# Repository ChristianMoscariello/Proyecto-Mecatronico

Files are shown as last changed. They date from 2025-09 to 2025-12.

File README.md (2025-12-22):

Logo Institucional

# Universidad Nacional de Lomas de Zamora – Facultad de Ingeniería

## Desarrollo de un dron multirrotor con inteligencia artificial embarcada para deteccion de personas y focos de incendio con cámara RGB y sensor térmico

---

## Introducción / Objetivo

En la Universidad Nacional de Lomas de Zamora, la Facultad de Ingeniería se dedica a la formación de profesionales en diversas ramas de la ingeniería. Este repositorio corresponde al proyecto desarrollado en el área de **Ingeniería Mecatrónica**, como parte del **Proyecto Final de Carrera**.

El objetivo de este proyecto es el **diseño, construcción e integración de un vehículo aéreo no tripulado (UAV) multirrotor**, capaz de ejecutar misiones autónomas de búsqueda mediante **sensado térmico, visión RGB e inteligencia artificial embarcada**, con transmisión de eventos a una estación de control terrestre.

El proyecto busca demostrar la **viabilidad técnica** de una plataforma de bajo costo orientada a tareas de detección temprana, priorizando estabilidad, confiabilidad y modularidad del sistema.

---

## Índice

- Descripción  
- Instrucciones de Uso  
- Tecnologías Utilizadas  
- Listado de Componentes  
- Esquemáticos  
- Fotos / Videos
- Carpetas del Proyecto  
- Autor  

---

## Descripción

Este proyecto se basa en el desarrollo de un **dron multirrotor tipo hexacóptero**, diseñado para realizar misiones autónomas de búsqueda y detección de eventos térmicos y visuales.

El sistema integra:

- Una **plataforma aérea** controlada por un piloto automático (Pixhawk comandado por un ESP32).
- Un **sistema de detección embarcado** basado en Raspberry Pi, encargado del procesamiento de imágenes RGB y térmicas mediante algoritmos de inteligencia artificial.
- Un **microcontrolador ESP32** que actúa como integrador del sistema, coordinando las comunicaciones entre los distintos subsistemas.
- Un enlace de **comunicación LoRa** para la transmisión de eventos relevantes hacia una estación base (*Estación Terrestre*).

La estación terrestre permite definir misiones, visualizar la trayectoria del dron y recibir notificaciones de eventos detectados, incluyendo su localización geográfica.

---

## Instrucciones de Uso

Para utilizar este proyecto, seguir los siguientes pasos generales:

**Paso 1:** Configurar y cargar el firmware correspondiente en el ESP32 y en la controladora de vuelo.

**Paso 2:** Preparar la Raspberry Pi con el sistema operativo y las dependencias necesarias para el procesamiento de imágenes y ejecución de los modelos de IA.

**Paso 3:** Conectar los sensores (cámara RGB y sensor térmico) y verificar su correcto funcionamiento.

**Paso 4:** Ejecutar la aplicación de la Estacion Terrestre desde una computadora en entorno Jupyter, estableciendo la comunicación con el dron mediante el adaptador USB - LoRa.

**Paso 5:** Definir una misión, cargarla en el sistema y realizar las pruebas de vuelo en un entorno controlado.

Asegurarse de contar con los componentes, herramientas y configuraciones detalladas en las secciones siguientes.

---

## Tecnologías Utilizadas

Este proyecto fue desarrollado utilizando las siguientes tecnologías:

### Robótica
- Controladores de vuelo para UAV (Pixhawk)
- Motores brushless y servomotores
- Plataforma multirrotor tipo hexacóptero

### Electrónica
- ESP32
- Sensor térmico (MLX90640)
- Cámara RGB (OV5647)
- Módulos de comunicación LoRa (SX1278)
- Controladores electrónicos de velocidad (ESC)

### Programación
- Python
- C / C++
- Scripts de control y procesamiento

### Plataformas
- MAVLink
- OpenCV
- ONNX Runtime

### Inteligencia Artificial
- Redes neuronales convolucionales
- YOLOv8 para detección de personas y fuego
- Procesamiento de visión por computadora

---

## Listado de Componentes

- Controladora de vuelo Pixhawk
- 6 x ESC de 30 A
- 6 x Motores brushless 2816
- 6 x Hélices 8x4.5 (3 giro derecho y 3 giro izquierdo)
- Batería LiPo 3S 5000 mAh
- Fuente step down XL4015 a 5V
- Microcontrolador ESP32
- Módulo LoRa SX1278
- Servo sg90
- Raspberry Pi  
- Sensor térmico MLX90640  
- Cámara RGB OV5647  
- Chasis impreso en 3D
- 6 x Brazos aluminio portamotores

Para el adaptador USB - LoRa de la base:
- Microcontrolador ESP32
- Módulo LoRa SX1278

---

## Esquemáticos

A continuación se presentan los esquemáticos y diagramas de diseño del sistema:

Esquema eléctrico del dron:

drone

Diagrama en bloques del dron:

Diagrama dron

Esquema eléctrico del adaptador USB-LoRa:

puente

Diagrama en bloques del adaptador USB-LoRa:

Diagrama puente

Diagrama en bloques estación terrestre:

Diagrama gs

## Fotos / Videos

En esta sección se incluyen imágenes y videos correspondientes al desarrollo y funcionamiento del proyecto:

- Fotografías del dron ensamblado


unnamed



fotodron2

- Imágenes de pruebas de vuelo

fotodronvual 

fotodronvula2 

fotodronvuela3

### Demostracion del funcionamiento

Seteo de la mision desde la estacion terrestre, verificacion de envios de datos, vuelo, analisis con resultado negativo y positivo (con imagenes capatadas por camara RGB e infrarroja)

https://drive.google.com/file/d/1ojA_1EPUBh213Cx6VwPE2h_yf2Y8xk58/view?usp=drive_link

https://youtu.be/2DbrhcWoiKQ

---

## Carpetas del Proyecto

La estructura del repositorio es la siguiente:

- **Adaptador USB-LoRa:** Codigo del adapatador para ESP32.
- **Camara termografica:** Codigo utilizado en el M5stick y Raspberry Pi.
- **Codigos camara:** Codigo utilizado para la camara RGB en Rapsberry Pi.
- **Entrenamiento IA:** Imagenes utilizada para entrenar la inteligencia artificial.
- **Esquemas electricos:** Esquemas de los componentes utilizados.
- **Estacion terrestre:** Versiones de la aplicacion de la estacion terrestre, codigo fuente a ejecutar en Jupyter.
- **Funcionando para final - comportameinto full:** Programas definitivos con el comportamiento correcto.
- **Funcionando para regularidad:** Programas con vuelo lineal a un punto.
- **Hojas de datos:** Hojas de datos de los componentes utilizados.
- **Informes:** Documentación técnica, informes, presentacion, cronogramas y material académico relacionado - leer informe e informe complementario.
- **Modelado 3D:** Archivos editables en SolidWorks con el ensamble y piezas del dron.  
- **Pixhawk:** Código fuente del sistema para ESP32.
- **Videos demostracion funcionamiento:** Imágenes y videos del desarrollo y pruebas, videos de misiones.  

---

## Autores

Este proyecto fue realizado por 

**Fernández Malenotti, Ignacio** 
fmalenotti.ignacio@gmail.com

**Moscariello, Christian**
chris_mosca7@hotmail.com

**Yacono, Emiliano**
emilianoyacono@gmail.com

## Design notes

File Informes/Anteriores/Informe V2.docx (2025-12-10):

Sistema de detección autónoma de personas y/o fuego

Para la implementación del sistema de visión y detección, se diseñó una arquitectura de software modular distribuida en tres bloques lógicos principales que operan de manera cooperativa. Esta estructura permite separar las tareas de adquisición de datos en tiempo real del procesamiento computacional intensivo, asegurando que el procesamiento pesado de las imágenes no detenga la ejecución del resto del sistema. Esto permite seguir recibiendo datos de los sensores y mantener la conexión fluida con el dron sin tener que esperar a que finalice cada inferencia de la inteligencia artificial.

Adicionalmente, esta división operativa ofrece una ventaja significativa en la gestión del software: el aislamiento de entornos. Cada código se ejecuta en su propio entorno virtual independiente, lo que evita conflictos entre versiones incompatibles de las mismas librerías. De esta manera, cada subsistema cuenta con las dependencias exactas que necesita, sin que las actualizaciones requeridas por el modelo de IA comprometan la estabilidad de los controladores de los sensores.

El flujo de información comienza en el nivel de hardware con el firmware del M5StickC, el cual actúa como un dispositivo de adquisición dedicado para el sensor térmico. En el siguiente nivel, ejecutándose sobre la Raspberry Pi, el Código 1 (Módulo de captura y análisis térmico) funciona como el orquestador principal: solicita los datos térmicos, captura las imágenes visuales RGB y realiza un primer filtrado de alertas basado en temperatura.

Finalmente, la integración entre la visión clásica y la inteligencia artificial se logra mediante un esquema asíncrono basado en el sistema de archivos. Cuando el Código 1 deposita una imagen en la carpeta compartida, se dispara automáticamente al Código 2 (Análisis con IA). Este último módulo procesa la imagen con el modelo YOLOv8 y, en caso de confirmar una detección positiva, emite las alertas correspondientes al sistema de control, cerrando así el ciclo de vigilancia autónoma detallado en el siguiente esquema global.

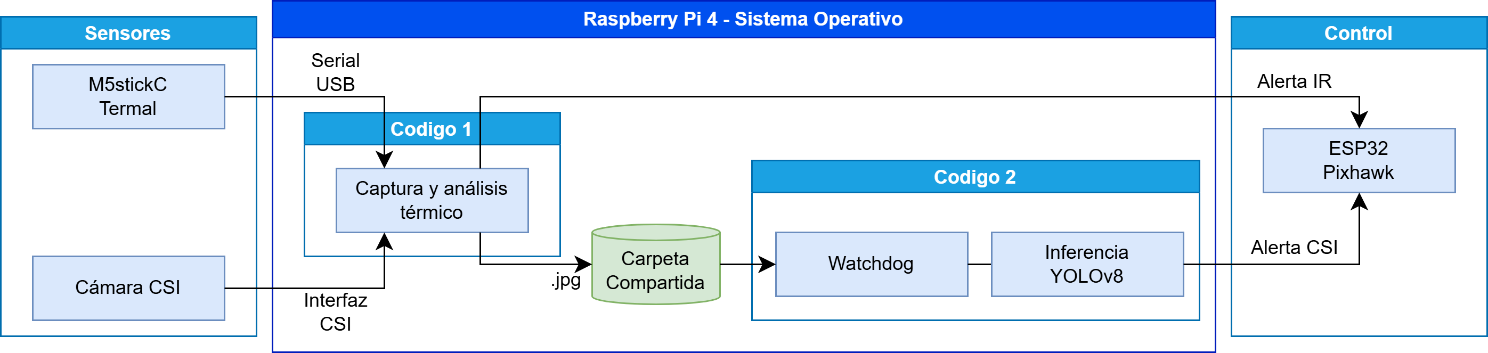
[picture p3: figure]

Descripción del firmware del M5StickC para adquisición térmica

El M5StickC utiliza su módulo ESP32-PICO interno para capturar y transmitir el cuadro térmico proveniente del sensor MLX90640. El firmware implementa un esquema de operación por solicitud (modo pull), en el cual la captura no se realiza de manera continua, sino únicamente cuando la Raspberry Pi envía el comando correspondiente a través del enlace serial USB. Esta lógica permite minimizar el procesamiento interno del dispositivo y evita generar datos innecesarios cuando no están siendo requeridos.

Inicializar pantalla, serial, bus I2C y sensor MLX90640

Al iniciar, el sistema configura la pantalla del M5StickC, el bus I2C utilizado para comunicarse con el sensor y la interfaz serial que enlaza el módulo con la Raspberry Pi. También se inicializa el MLX90640 con los parámetros de funcionamiento seleccionados: modo intercalado, resolución de 18 bits y una frecuencia de actualización de 2 Hz. En caso de que el sensor no responda, el dispositivo detiene su ejecución y muestra un mensaje de error para evitar el envío de información incorrecta.

Iniciar captura térmica

Una vez completada la configuración, el M5StickC permanece a la espera de un comando entrante. Si la Raspberry Pi envía la cadena "GET_FRAME", el firmware inicia la lectura completa del sensor y obtiene la matriz de 768 valores de temperatura. Luego, estos datos se redondean a dos decimales y se empaquetan en un documento JSON que contiene un único arreglo con todas las mediciones, manteniendo el orden original de la matriz del sensor.

Limpiar buffer serial y enviar JSON

Para asegurar una transmisión limpia, el firmware limpia el buffer serial antes de enviar la respuesta y encapsula el mensaje JSON entre dos delimitadores (#START y #END). Esto permite que la Raspberry Pi detecte con precisión el inicio y el fin del paquete, incluso si el flujo serial contiene ruido o interrupciones temporales. Finalmente, el dispositivo actualiza la pantalla para indicar el envío y vuelve al estado de espera hasta recibir el próximo comando.

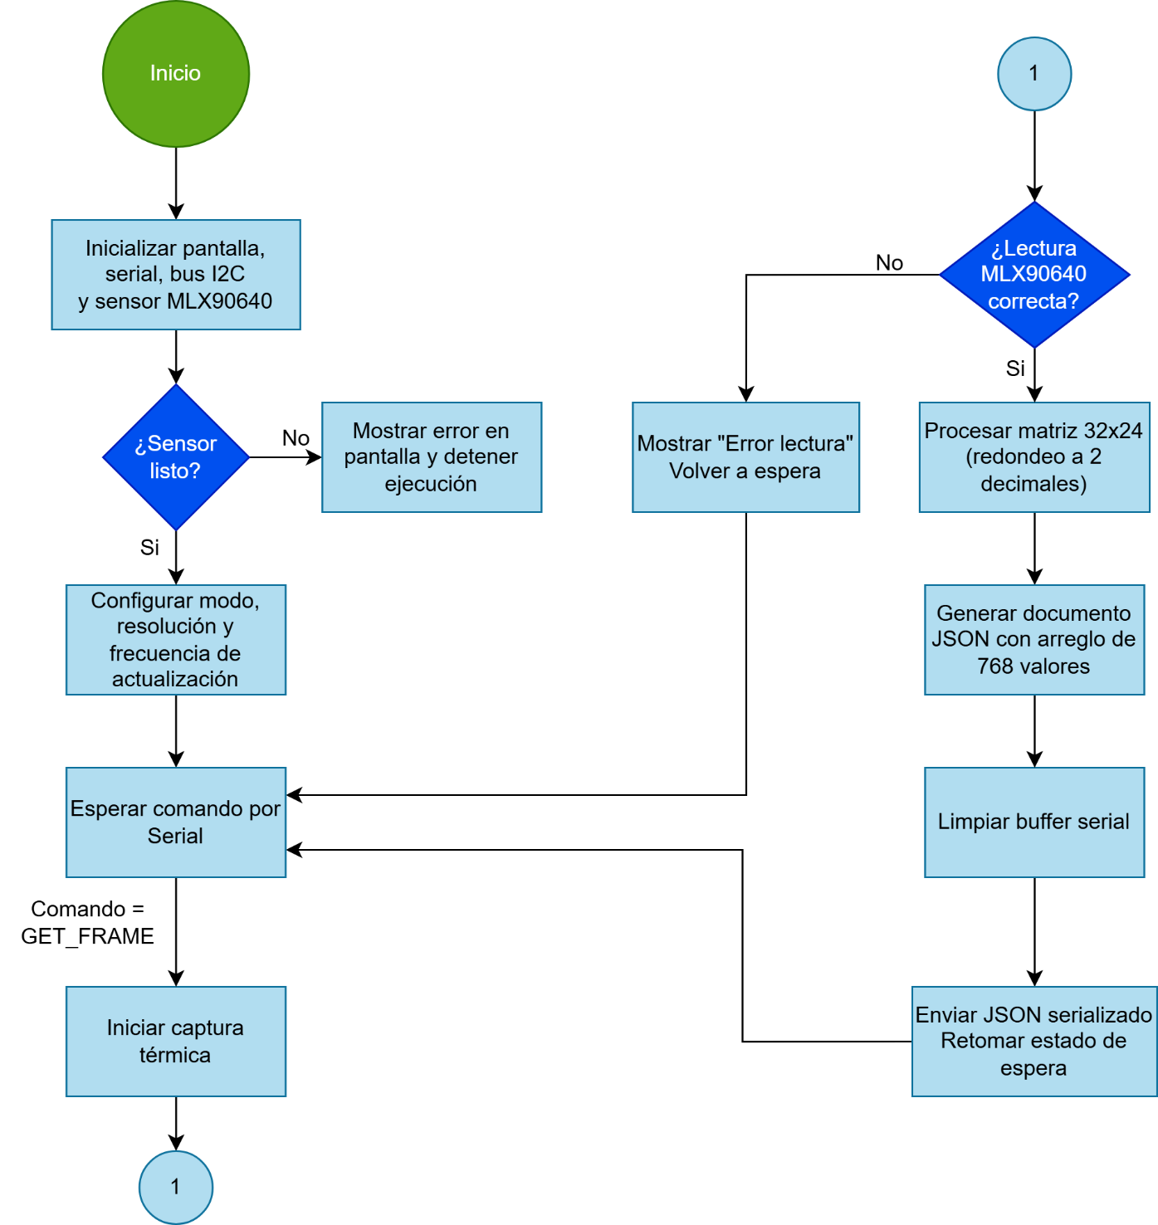
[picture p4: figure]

Descripción técnica del módulo de captura y análisis térmico

El módulo de captura y análisis térmico, implementado en el programa “codigo1_camaras_v2.py”, constituye el núcleo funcional del subsistema de visión del dron, integrando captura de imágenes, análisis térmico en tiempo real y comunicación bidireccional con los dispositivos embarcados (M5StickC con sensor térmico y ESP32 para las órdenes de vuelo). En su diseño se prioriza la fiabilidad operativa, la trazabilidad de eventos y la capacidad de ejecutar detección autónoma sin intervención del operador.

Inicialización Serial/Carpetas/Cámara

El código se estructura en torno a una clase de configuración centralizada que define todos los parámetros relevantes para la ejecución: puertos seriales, velocidades de comunicación, características de la cámara CSI, umbrales térmicos para la detección de personas e incendios, y rutas de almacenamiento. Esta centralización permite mantener un control claro sobre los elementos críticos del sistema.

Una vez iniciada la aplicación, el sistema crea y valida automáticamente las carpetas de trabajo y habilita un esquema de registro persistente de métricas y eventos, pensado para documentar tanto condiciones normales de funcionamiento como situaciones de error.

Modo de toma de imágenes

En cuanto a la adquisición sensorial, el módulo establece dos canales de comunicación independientes. Por un lado, se conecta al M5StickC con su sensor MLX90640 integrado, responsable de transmitir matrices térmicas de 32×24 píxeles, encapsuladas en formato JSON. Por el otro, se vincula con la ESP32, que puede iniciar el proceso de captura mediante el comando STABLE o recibir mensajes de alerta cuando el sistema identifica una anomalía térmica. Ambos enlaces operan con tolerancia a fallos y emplean hilos independientes cuando es necesario, garantizando que la recepción de comandos no interfiera con el procesamiento de imágenes.

El procesamiento térmico constituye el corazón computacional del módulo. Cada frame recibido es sometido a un filtrado de mediana para reducir ruido y mejorar la coherencia espacial de la matriz. Luego se ejecuta un análisis basado en segmentación por umbral adaptativo: el sistema determina dinámicamente la temperatura de fondo y la contrasta con rangos característicos para personas y focos de incendio. Los rangos de temperatura y área utilizados para discriminar entre personas y focos de incendio se definen durante la inicialización del sistema y provienen de pruebas de campo realizadas previamente, lo que permite adaptar el algoritmo a condiciones reales.

En paralelo a la recepción y procesamiento del frame térmico, el software coordina la toma de imágenes RGB con una cámara OV5647 de 8MP y las mismas son guardadas con el mismo sello temporal que la térmica para facilitar su análisis conjunto. Las imágenes RGB se almacenan en la carpeta “imágenes_visual” para que sean relevadas por el código que analizará a las mismas utilizando inteligencia artificial.

Resultados del análisis térmico

Se utilizan técnicas de etiquetado de componentes conectados para identificar regiones candidatas, evaluando su área y delimitándolas con recuadros que representan las detecciones en la matriz térmica. Esta metodología permite operar incluso en condiciones de ruido térmico elevado y evita falsos positivos derivados de objetos ambientales cálidos pero no relevantes.

Una vez identificadas las regiones de interés, el módulo genera una imagen térmica interpretada mediante un mapa de calor (heatmap), señalando visualmente las detecciones mediante los recuadros codificados por color. Finalmente, cuando el sistema determina la presencia de una persona o un posible foco ígneo, se activa el protocolo de alerta hacia la ESP32, enviando una cadena JSON minimalista que sirve como disparador para acciones de navegación o marcación de eventos en el dron.

El ciclo de operación permite dos modos de activación: captura manual mediante teclado o activación remota desde la ESP32. Esto habilita tanto pruebas en laboratorio como funcionamiento autónomo durante un vuelo real. Cada ciclo concluye retornando un estado de éxito o error y dejando registrada toda la actividad en los archivos de log correspondientes.

En conjunto, este módulo implementa una arquitectura de software orientada a la confiabilidad y la detección temprana, combinando visión térmica, control asincrónico de hardware y generación de evidencia visual. Es el componente responsable de transformar datos brutos del sensor infrarrojo en información estructurada y accionable, funcionando como la primera etapa de interpretación del entorno en el sistema completo del dron.

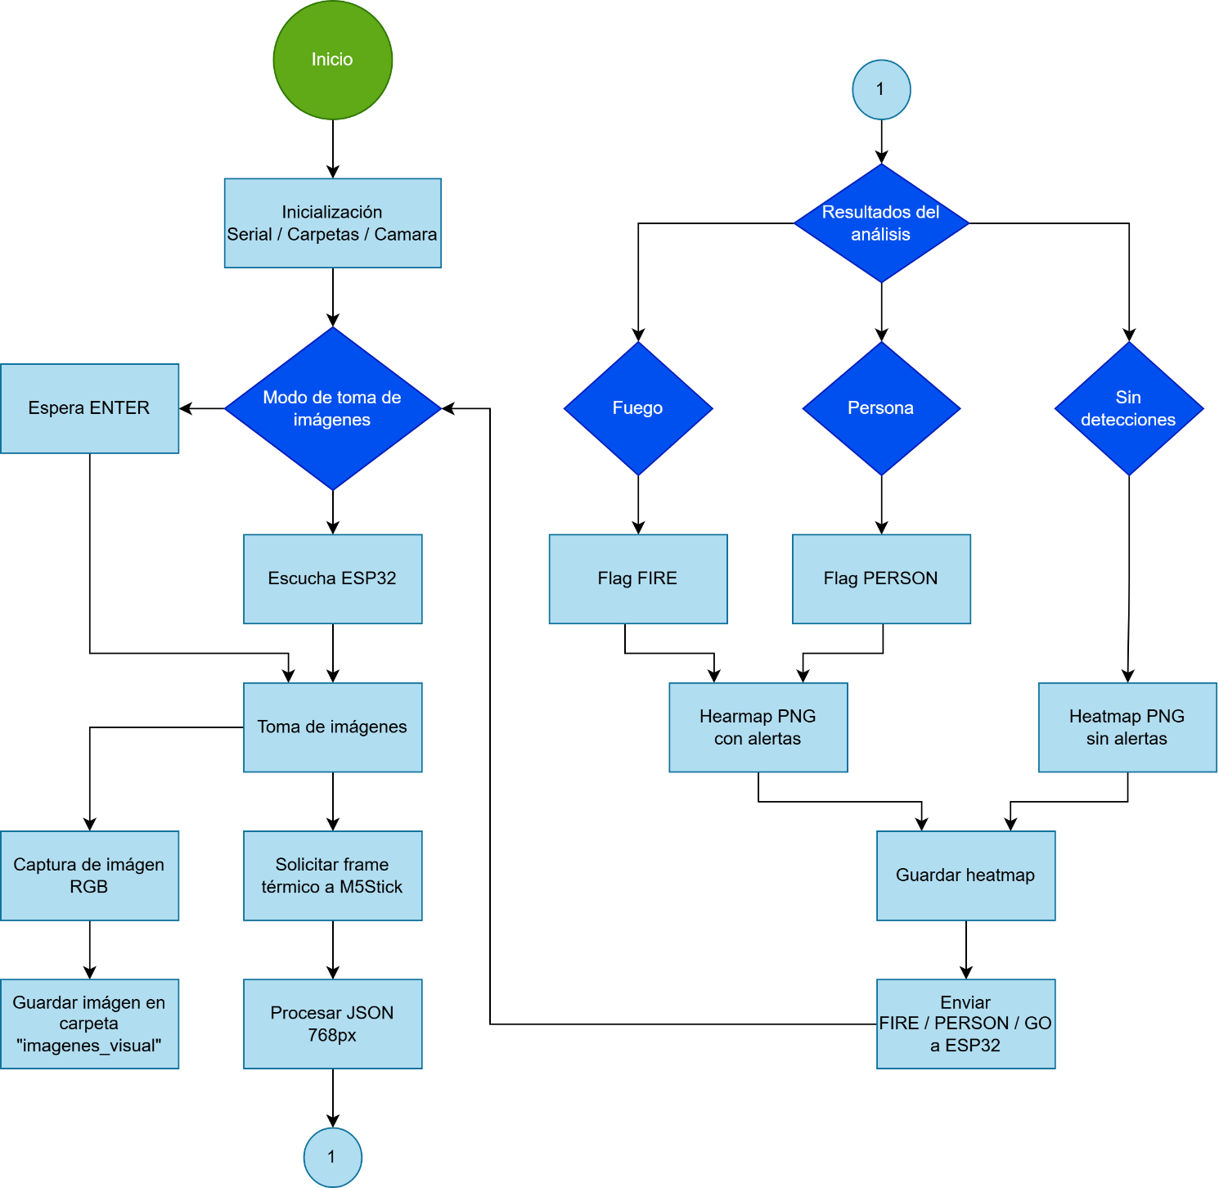
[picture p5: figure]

Descripción técnica del módulo de análisis de imágenes con inteligencia artificial

El segundo módulo del sistema, codigo2_ia_v3.py, cumple el rol de núcleo inteligente del pipeline general. Mientras el Código 1 se ocupa de adquirir imágenes RGB y almacenarlas de manera ordenada, este módulo funciona como un observador activo que espera la llegada de esos archivos para someterlos a un análisis automático mediante un modelo de detección basado en YOLOv8 exportado a ONNX. De esta manera, Código 2 permite cerrar el ciclo completo: captura, procesamiento inteligente y emisión de alertas al dron o al sistema embebido encargado de actuar en consecuencia.

Un aspecto clave del diseño es que todo el análisis de imágenes se realiza de manera local, sin depender de servicios externos ni de una conexión estable a Internet. Esto responde a una limitación propia del sistema: la comunicación entre el dron y la base se establece mediante LoRa, un protocolo de largo alcance pero muy baja tasa de transferencia, insuficiente para enviar imágenes o ejecutar análisis de imágenes de manera remota. Al ejecutar la inteligencia artificial directamente en la Raspberry embarcada sobre el dron, mismo puede operar de forma autónoma y generar alertas inmediatas sin necesidad de enlaces WiFi o satelitales, lo que mejora la robustez del sistema y lo vuelve apto para entornos aislados o con conectividad limitada.

Configurar sistema (carpetas, paths, clases)

El programa inicia estableciendo una configuración centralizada que define los directorios relevantes, los parámetros y el modelo a utilizar. A diferencia del primer módulo, aquí el objetivo no es solo verificar y organizar carpetas, sino también garantizar un entorno de ejecución preparado para alojar tanto las imágenes procesadas como los registros de funcionamiento.

Esta etapa crea las carpetas necesarias, carga el nombre del modelo ONNX y fija los umbrales mínimos de confianza para descartar predicciones irrelevantes. Al igual que Código 1, este módulo también mantiene comunicación con la ESP32, enviando alertas de detección o indicaciones para continuar la exploración.

Carga de modelo YOLOv8 ONNX

El corazón del módulo se concentra en la clase AnalizadorIA, encargada de cargar el modelo YOLOv8 en formato ONNX y llevar adelante el flujo completo: desde la preparación de la imagen, pasando por el análisis del modelo, hasta la interpretación final de las detecciones.

Durante el proceso, las imágenes se redimensionan, normalizan y convierten al formato requerido por el modelo. Luego, las predicciones se reescalan al tamaño original y se construyen los recuadros delimitadores junto con sus etiquetas correspondientes.

Una decisión de diseño destacada es la definición explícita de las clases (“Persona”, “Fuego”, “Humo”), agrupando fuego y humo bajo una misma categoría de alerta (FIRE) para simplificar la comunicación operativa con el dron.

Iniciar vigilancia (watchdog en carpeta)

Sobre este analizador se apoya el componente responsable de reaccionar a los eventos del sistema de archivos. Utilizando la biblioteca watchdog, el módulo monitoriza en tiempo real la carpeta de salida del Código1. Cada vez que aparece una nueva imagen, el código procesa el archivo, lo somete al análisis del modelo y genera una imagen anotada con las detecciones encontradas. Esta imagen se guarda con un registro de fecha y hora preciso, lo que facilita la trazabilidad y el alineamiento temporal con los registros del resto del sistema.

Resultados del análisis

La lógica de alertas también reside en este módulo. Cuando no se detectan objetos relevantes, el sistema informa a la ESP32 mediante el mensaje “GO”, manteniendo el flujo de confirmaciones del estado general. Por el contrario, si se identifican personas, fuego o humo, se emiten alertas específicas (“PERSON” o “FIRE”), habilitando al dron a reaccionar de acuerdo con la situación.

Finalmente, el ciclo completo del sistema se encapsula en la clase SistemaIA. Una vez en ejecución, el módulo entra en un estado de escucha permanente y solo se detiene ante una interrupción explícita del usuario. Al finalizar, todos los recursos se liberan de manera ordenada, asegurando un cierre limpio tanto de la conexión serial como del proceso del watchdog.

En conjunto, este módulo observa, interpreta y actúa, conectando el análisis visual avanzado con una lógica operacional liviana pero efectiva. Su diseño apunta a la fiabilidad y a la eficiencia, respetando el flujo general del proyecto y complementando las capacidades del Código1 para conformar un sistema coherente de vigilancia automática.

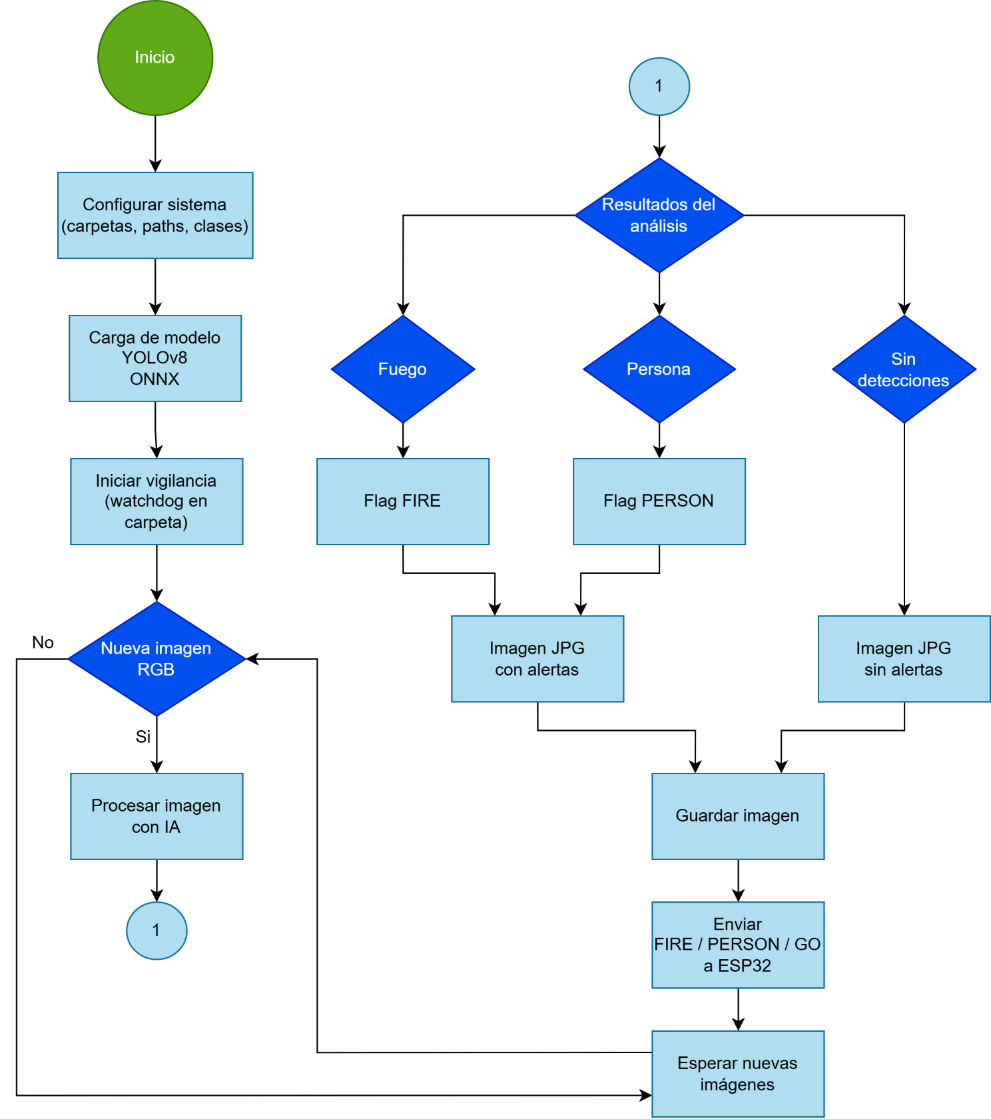
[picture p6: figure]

Facultad de Ingeniería Universidad Nacional de Lomas de Zamora

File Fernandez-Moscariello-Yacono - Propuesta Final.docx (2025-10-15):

PROYECTO FINAL MECATRONICA

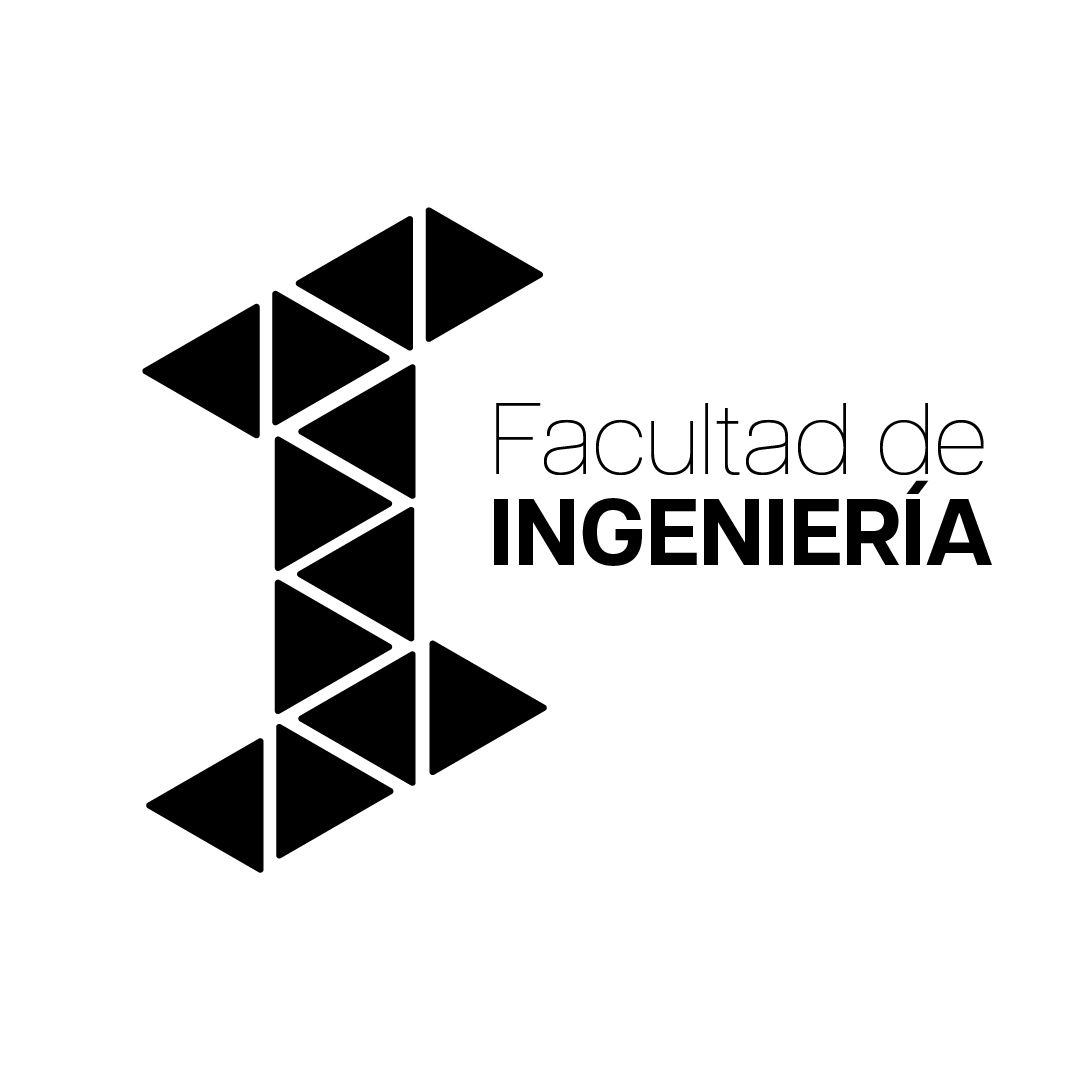
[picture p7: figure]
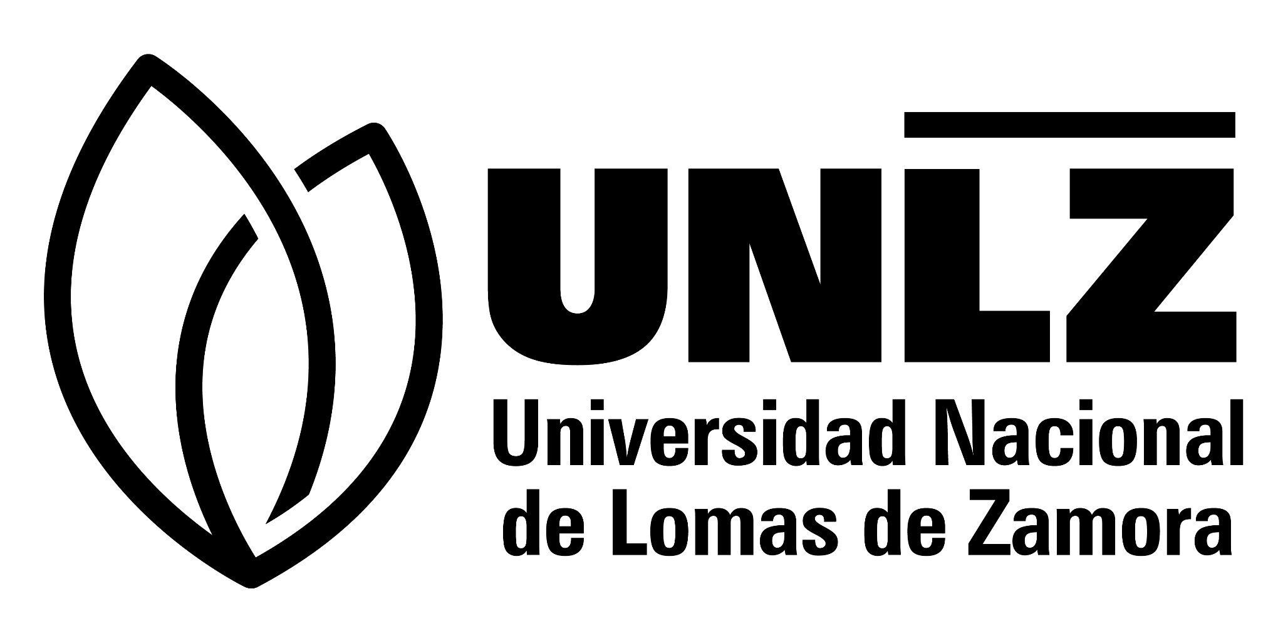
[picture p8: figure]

Profesores:

Ing. Blanca, Ezequiel

Ing. Lukaszewicz, Cristian Leandro

Ing. Szombach, Juan Ignacio

Alumnos:

Fernandez Malenotti, Ignacio

Moscariello, Christian

Yacono, Emiliano

# Propuesta Final

## Título del Proyecto

Dron Autónomo para Detección de Incendios y Rescate de Personas

## Motivación y Antecedentes

Durante el verano, zonas de parques nacionales y áreas de montaña enfrentan dos problemáticas críticas:

1. La aparición de focos de incendio, que pueden propagarse rápidamente debido a la vegetación seca.
2. El extravío de personas en zonas de difícil acceso, como bosques y áreas montañosas.

Actualmente, la cobertura de grandes extensiones con personal reducido dificulta las tareas de vigilancia, control y rescate. Esto retrasa la respuesta inicial ante un incendio o la localización de personas, aumentando riesgos y daños. Además, el coste de patrullaje de un helicóptero es elevado y su espacio aéreo de observación acotado.

## Descripción de la Propuesta

Se propone el desarrollo de un prototipo de dron autónomo a escala, capaz de:

1. Detectar visual y térmicamente focos de incendio en su etapa inicial.
2. Localizar personas extraviadas mediante análisis de imagen e infrarrojo.
3. Transmitir coordenadas precisas a los equipos de intervención.
4. Transportar pequeñas cargas, como materiales para iniciar la extinción de focos o suministros de supervivencia y primeros auxilios.

El proyecto se centra en mostrar la viabilidad técnica de un sistema aéreo no tripulado para inspeccionar grandes superficies de forma rápida y eficiente, incluso en zonas de difícil acceso terrestre.

## Alcance

En la presentación final se podrá mostrar:

1. El dron volando y detectando de forma representativa un foco de incendio o una persona.
2. El sistema de sujeción de pequeñas cargas (prototipo).
3. Transmisión de coordenadas y visualización de imágenes térmicas o simuladas.

Limitaciones:

- La capacidad de carga estará restringida por el tamaño y peso del dron prototipo.
- La parte de extinción o entrega de suministros será demostrativa, no a escala real por razones de peso y seguridad.

- No está contemplada la navegación en interiores ni que pueda sortear autónomamente obstáculos, puesto que no contará con sensor de tipo radar 3D debido a restricciones monetarias y temporales en el desarrollo.

Escenario de uso

- Parques provinciales, nacionales, etc., campos privados y todo tipo de establecimiento donde se requiera patrullaje activo en época de peligro de incendios.
- Parques provinciales, nacionales, etc. y cualquier ubicación donde se practique treking u otra actividad que lleve a personas a áreas remotas y de difícil acceso, dónde puedan perderse o sufrir un accidente y por lo consiguiente necesiten ser ubicadas en el menor periodo de tiempo posible.
- Para un mejor aprovechamiento de la tecnología se propone el uso de múltiples drones, con la finalidad de poder rastrillar simultáneamente mayor superficie de terreno.

## Docentes para Consultas

- Catedra de procesamiento de señales: uso de filtros y diversas formas de usar sensores para obtener señales en su forma más representativa.
- Catedra de mecánica de los fluidos: cálculo de fuerzas de empuje y sustentación.
- Catedra de modelado y dinámica de sistemas mecánicos: modelado de estructuras, fuerzas y cargas

Especificación de requerimientos

- Auto pilotaje: Mediante un sistema de coordenadas GPS dinámico y un acelerómetro, el dron deberá realizar una ruta de vuelo tipo rastrillaje y volver al punto de origen al finalizar.
- Procesamiento de imágenes térmicas: Utilizando un sensor IR deberá ser capaz de detectar focos de anormalidad térmica.
- Procesamiento de imágenes RGB: Utilizando una cámara y una inteligencia artificial correctamente entrenada alojada en un Raspberry pi, el dron deberá detectar de qué se trata el foco de anomalia térmica (principio de incendio, persona perdida, animal).
- Transporte de kit de auxilio: En caso de que se este buscando una persona y la misma sea encontrada, mediante un sistema tipo gripper/dropper se le proporcionará un kit de primera contingencia.

Diseño funcional

Arquitectura general:

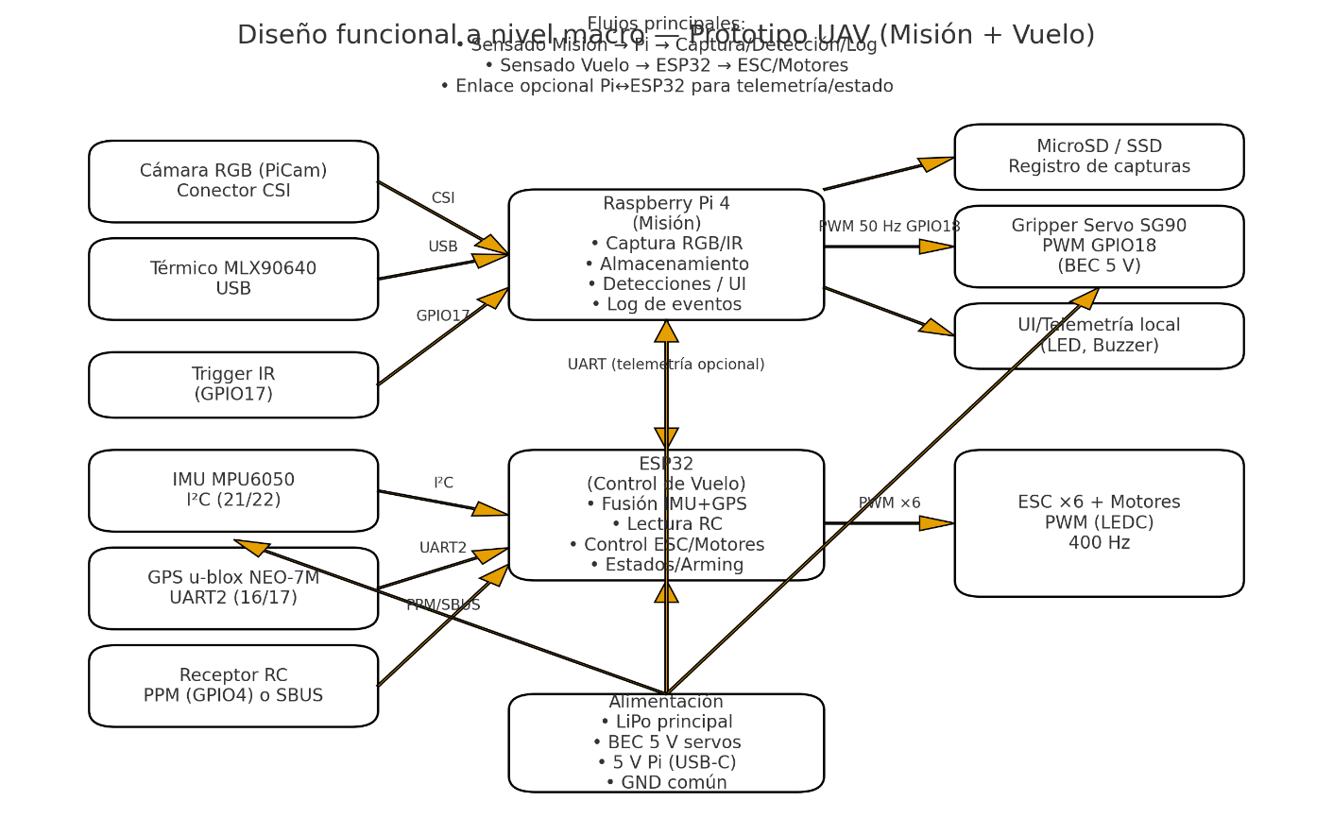
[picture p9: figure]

Conexionado individual:

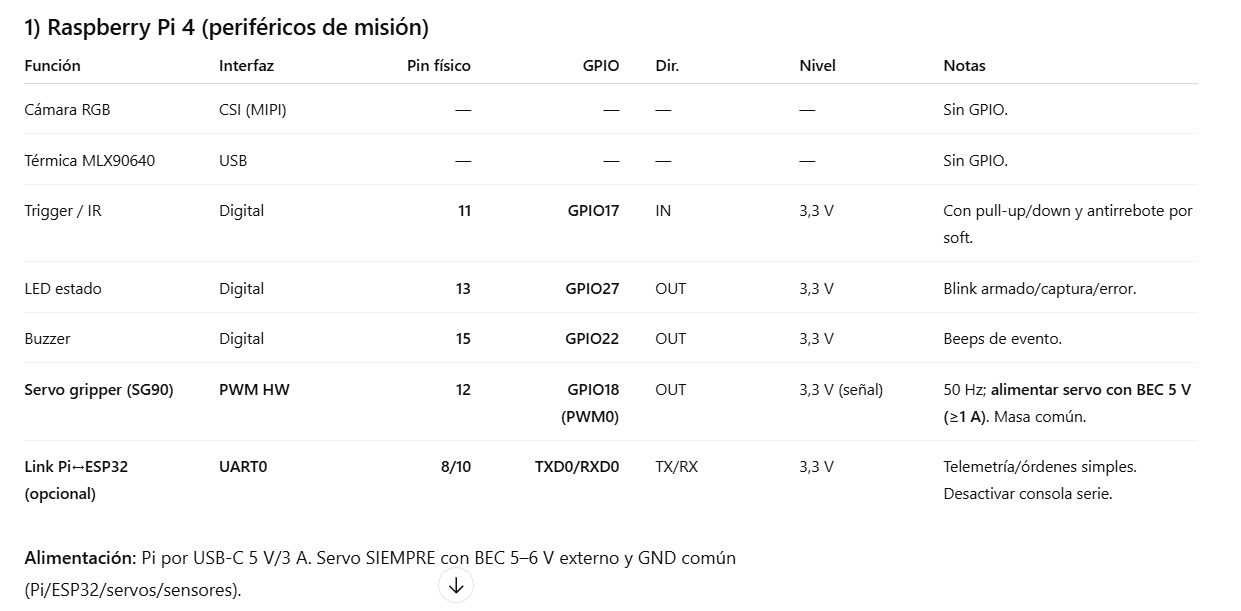
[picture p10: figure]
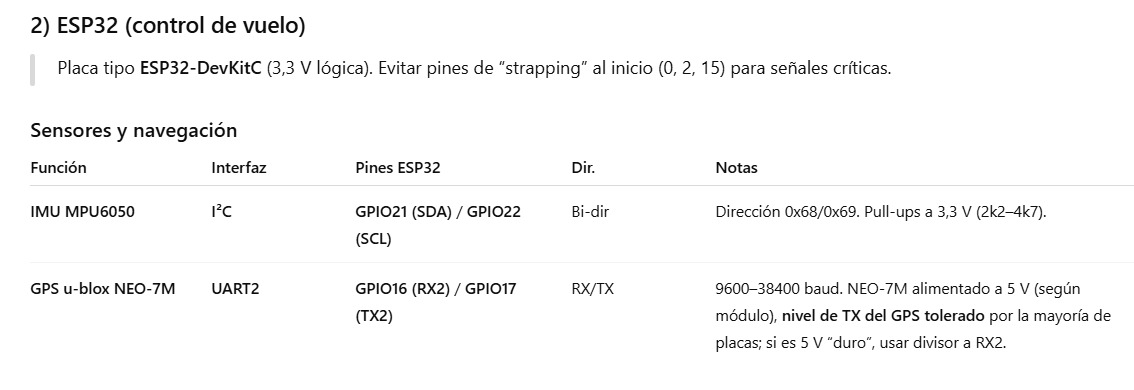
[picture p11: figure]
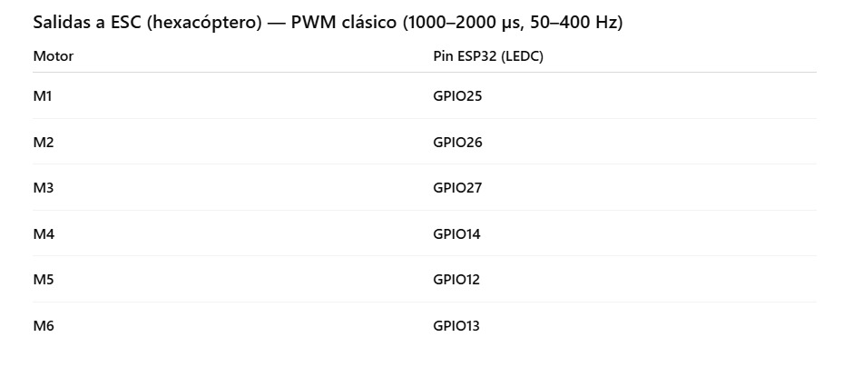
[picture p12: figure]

Lista de materiales y costos

Ítem | Cantidad | Precio unitario | Precio total
Motor brushless + ESC 30A + Helice | 6 | 50000 | 300000
Batería LiPO 3S | 1 | 70000 | 70000
ESP32 | 1 | 10000 | 10000
Kit NAZA M V2 | 1 | 160000 | 160000
Estructura (caños aluminio + placas conectoras) | 1 | 40000 | 40000
Cámara térmica IR | 1 | 180000 | 180000
Raspberry pi 4 | 1 | 100000 | 100000
Cámara RGB | 1 | 35000 | 35000
Rollo filamento PETG | 1 | 18000 | 18000
Miscelaneos (tornillería, cables, luces) | 1 | 15000 | 15000
Total | | | 928000

Universidad Nacional de Lomas de Zamora Facultad de Ingeniería

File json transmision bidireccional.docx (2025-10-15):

PC → Dron (Comandos enviados desde la estación)
Comando (t) | Ejemplo d completo | Descripción
MISSION_COMPACT | json { "p": [[-34.6037, -58.3816], [-34.6040, -58.3820], [-34.6030, -58.3830]], "h": [-34.6035, -58.3810], "a": 30, "s": 10, "event_action": "VOLVER" } | Envía misión compacta con polígono, HOME, altitud, espaciamiento y acción tras evento
RETURN | {} | Ordena al dron regresar a HOME
ARM | {} | Arma el dron para vuelo
DISARM | {} | Desarma el dron
TRIM | json { "accel": 128, "roll_lr": 128, "roll_fb": 128, "rudder": 128, "switch": 128 } | Envía trims configurados desde la GUI
GET_TRIMS | {} | Solicita los valores de trims al dron
GRIPPER | { "state": "OPEN" } | Abre o cierra el gripper

Dron → PC (Mensajes recibidos por la estación)
Comando (t) | Ejemplo d completo | Descripción
TELEMETRY | json { "lat": -34.6037, "lon": -58.3816, "alt": 32, "speed": 12, "heading": 90, "battery": 85, "status": "ARMED", "current_wp": 2, "total_wp": 5 } | Telemetría en tiempo real del dron
STATUS | { "message": "Misión iniciada" } | Estado general o respuesta de comando
WP_REACHED | { "wp_number": 2 } | Indica que se alcanzó un waypoint
DEBUG | { "message": "Sensor OK" } | Mensaje de depuración del dron
FIRE | { "lat": -34.6040, "lon": -58.3820 } | Detección de fuego, marcador en mapa
PERSON | { "lat": -34.6050, "lon": -58.3830 } | Detección de persona, marcador en mapa
TRIM_DATA | json { "accel": 128, "roll_lr": 128, "roll_fb": 128, "rudder": 128, "switch": 128 } | Respuesta con valores actuales de trims

Raspberry ➜ ESP32
Comando (t) | Ejemplo d completo | Descripción
FIRE | {} | Detección de fuego
PERSON | {} | Detección de persona

Ejemplos:

{ "t": "FIRE", "d": { }, "ts": 0}

{ "t": "PERSON", "d": { }, "ts": 0}

ts: timestamp, enviar cero

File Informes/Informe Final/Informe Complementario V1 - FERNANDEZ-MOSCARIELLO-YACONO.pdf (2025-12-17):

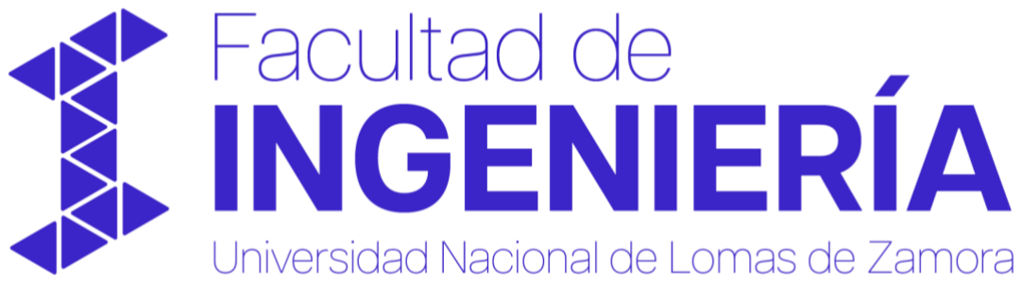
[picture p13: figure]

# PROYECTO EN INGENIERÍA MECATRÓNICA

# Dron autopilotado con detección de fuego y personas mediante procesamiento IA de cámaras INFORME COMPLEMENTARIO

## Integrantes:

- FERNANDEZ MALENOTTI, Ignacio | DNI: 42.043.463
- MOSCARIELLO, Christian | DNI: 37.053.307
- YACONO, Emiliano | DNI: 34.485.253

## Docentes:

## - Ing. Blanca, Ezequiel - Ing. Lukaszewickz, Cristian - Ing. Szombach, Juan

### Facultad de Ingeniería

Universidad Nacional de Lomas de Zamora

Índice

Ya teniendo en claro qué debe hacer el gripper se establecen una serie de

1.Introducción

En este informe complementario se buscará dar una mirada más teórica a la constitución física del dron: se analizarán temas como qué es un dron, qué tipos existen, por qué vuelan, qué fuerzas interactúan en los mismos y demás. Se ejemplifica con el prototipo construido y se repasan técnicas y diseño del mismo.

1.1. Contexto del proyecto

En los últimos años, los vehículos aéreos no tripulados (UAV) han adquirido una relevancia creciente en aplicaciones de monitoreo, inspección y asistencia en entornos de difícil acceso. En particular, los drones multirrotor ofrecen ventajas significativas en términos de maniobrabilidad, despegue vertical y capacidad de vuelo estacionario. Todo esto, enfocado hacia la búsqueda de personas desaparecidas e inicios de focos de incendio.

1.2. Objetivo general del sistema

El objetivo general del sistema desarrollado es diseñar e implementar un dron multirrotor capaz de ejecutar misiones autónomas de exploración dentro de un área delimitada, incorporando capacidades de detección de eventos y actuación física sobre el entorno.

1.3. Metodología de desarrollo

El desarrollo del prototipo se realizó siguiendo una metodología de diseño iterativa, propia de un proyecto experimental, en la cual se combinaron etapas de análisis teórico, selección de componentes, fabricación de piezas y validación mediante pruebas prácticas.

### 2. Concepto general de vehículo aéreo no tripulado (UAV)

2.1. Definición de dron / UAV

Un vehículo aéreo no tripulado (Unmanned Aerial Vehicle), es una aeronave capaz de funcionar sin un piloto a bordo, su control puede realizarse de manera remota u operar de forma autónoma utilizando sensores y sistemas electrónicos on board.

En términos de ingeniería, un UAV forma parte de un sistema más amplio que incluye sensores, actuadores, sistemas de control, comunicación y una estructura física diseñada para soportar las cargas aerodinámicas y operacionales durante el vuelo.

2.2. Clasificación de drones

Los UAV pueden clasificarse según distintos criterios, siendo uno de los más relevantes el tipo de plataforma aérea utilizada para generar sustentación y control de vuelo.

2.2.1. Ala fija

Los drones de ala fija generan sustentación a partir del movimiento relativo del aire sobre la superficie alar, de manera similar a una aeronave convencional. Este tipo de plataformas se caracteriza por una alta eficiencia energética en vuelos de larga distancia y mayor autonomía.

Sin embargo, requieren una velocidad mínima para mantenerse en vuelo, lo que implica la necesidad de pistas de despegue, catapultas o sistemas de lanzamiento, lo que implica también, una pista con sensores y una mayor complejidad al momento de despegue/aterrizaje.

Este tipo de drones no permiten vuelo estacionario.

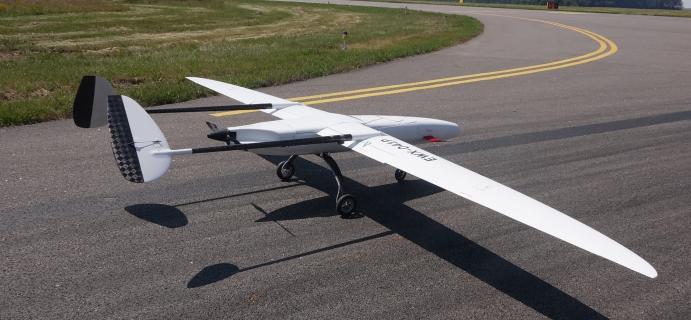
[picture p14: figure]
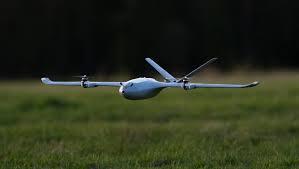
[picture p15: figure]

Dron de ala fija.

2.2.2. Multirrotores

Los drones multirrotor utilizan múltiples hélices dispuestas alrededor de un chasis para generar empuje vertical de manera directa. El control del movimiento se logra mediante la variación de la velocidad angular de cada motor, permitiendo controlar los ejes de roll, pitch y yaw sin superficies aerodinámicas móviles (flaps, alerones como poseen los drones de ala fija).

Entre sus principales características se destacan la capacidad de despegue y aterrizaje vertical, el vuelo estacionario y una elevada maniobrabilidad, lo que los hace especialmente adecuados para misiones de precisión y operación en espacios reducidos.

Los drones con redundancia de motores (6 u 8) pueden llegar a continuar un vuelo o hacer un aterrizaje de emergencia sin suponer una caída inmediata en caso de que alguno de los mismos falle.

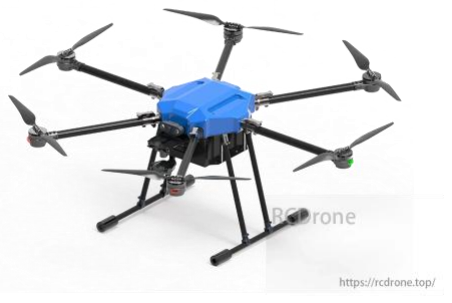
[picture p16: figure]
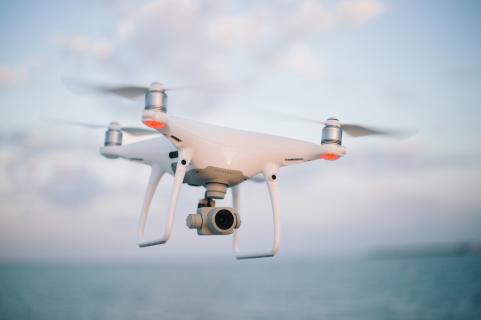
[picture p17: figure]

Dron multirrotor.

2.2.3. Comparación y elección del multirrotor

Si bien los UAV de ala fija presentan ventajas en términos de eficiencia y alcance, sus limitaciones operativas los hacen poco adecuados para misiones que requieren vuelo estacionario, maniobras precisas y operación en áreas delimitadas.

En el contexto del presente proyecto, orientado a tareas de exploración, detección y asistencia en un área específica, la configuración multirrotor resulta la opción más adecuada, ya que permite un control preciso de la posición y la capacidad de detenerse sobre un punto de interés.

Característica | Ala fija | Multirrotor
Despegue vertical | No | Si
Vuelo estacionario | No | Si
Autonomía | Alta (1 motor) | Baja (+ 4 motores)
Precisión | Baja | Alta
Complejidad mecánica | Alta | Media
Adecuado para ayuda | Limitado por precisión | Óptimo
2.3. Aplicaciones típicas (búsqueda, monitoreo, rescate)

Los UAV multirrotor se emplean ampliamente en aplicaciones donde se requiere acceso rápido, operación remota y adquisición de información en tiempo real. Entre las aplicaciones más relevantes se encuentran las tareas de búsqueda y rescate, monitoreo ambiental, inspección de estructuras inseguras y asistencia en situaciones de emergencia.

La capacidad de integrar sensores especializados para la tarea y realizar misiones autónomas convierte a estas plataformas en herramientas eficaces y eficientes para la exploración de zonas de difícil acceso o potencialmente peligrosas para humanos.

### 3. Fundamentos físicos del vuelo

El vuelo de un dron multirrotor se basa en la generación de empuje aerodinámico mediante hélices rotativas que interactúan con el aire circundante. Desde el punto de vista de la aerodinámica, una hélice puede modelarse como un disco actuador (teorema de Froude y Betz) que imparte una variación de cantidad de movimiento a una masa de aire, generando una fuerza de reacción que permite sostener y maniobrar el vehículo

A diferencia de las aeronaves de ala fija, donde la sustentación se produce por el desplazamiento horizontal, en los multirrotores el empuje se genera principalmente en dirección normal al plano de rotación de las hélices, permitiendo el vuelo estacionario.

3.1. Principio de sustentación

En drones multirrotor, la sustentación está directamente asociada al empuje producido por las hélices, el cual puede analizarse mediante la teoría de cantidad de movimiento aplicada a un disco actuador.

3.1.1. Flujo de aire y generación de empuje

La hélice puede considerarse un mecanismo destinado a generar una fuerza capaz de mover un vehículo inmerso en un fluido. Desde el punto de vista físico, se trata de un ala que gira alrededor de un eje, impulsada por un motor, impartiendo un pequeño incremento de velocidad a una gran masa de aire que atraviesa el plano de rotación

Según la segunda ley de Newton, el empuje generado por la hélice es consecuencia del cambio de cantidad de movimiento del aire:

T = m ∗ ΔV

donde el caudal másico de aire atravesando el disco depende del área del mismo y de la velocidad inducida en el flujo.

3.1.2. Diferencia de presiones

El modelo de disco actuador establece que, al atravesar el plano de la hélice, el aire experimenta un salto de presión. Aguas arriba del disco, el aire posee una presión y velocidad determinadas, mientras que al cruzar el disco se agrega energía al flujo en forma de un incremento de presión ∆p, asociado al trabajo realizado por el motor

El empuje generado por el disco puede expresarse como:

T = A ∗ Δp

siendo A el área del disco actuador. Este enfoque permite vincular directamente el empuje con la variación de presión inducida por la hélice.

3.1.3. Relación con hélices rotativas

Una hélice real no es un disco continuo, sino un conjunto de palas que pueden interpretarse como elementos de ala rotativa. Cada sección radial de la pala contribuye al empuje total, y la suma de estas contribuciones a lo largo del radio reproduce el comportamiento global del disco actuador

La teoría de pala-elemento confirma que una hélice eficiente es aquella que transfiere poca energía cinética a una gran masa de aire, minimizando pérdidas.

3.2. Fuerzas actuantes sobre el dron

Durante el vuelo, el dron se encuentra sometido a un conjunto de fuerzas externas que determinan su equilibrio y movimiento.

3.2.1. Sustentación (Lift)

En el caso del multirrotor, la sustentación se identifica con el empuje total generado por las hélices. Esta fuerza actúa aproximadamente normal al plano de rotación y es consecuencia directa de la aceleración del aire hacia abajo producida por los rotores.

3.2.2. Peso

El peso es la fuerza gravitatoria que actúa sobre el dron y se expresa como:

P = m ∗ g

Esta fuerza incluye la masa de la estructura, los sistemas electrónicos, la batería y la carga útil

3.2.3. Arrastre (Drag)

El arrastre aerodinámico se opone al movimiento relativo del dron respecto al aire. Si bien su influencia es reducida en vuelo estacionario, cobra importancia durante desplazamientos horizontales y maniobras dinámicas.

3.2.4. Empuje (Thrust)

El empuje es la fuerza generada por las hélices al impartir energía al flujo de aire. Desde el punto de vista del modelo de cantidad de movimiento, el empuje total se obtiene del balance entre el flujo de masa y la variación de velocidad inducida en el aire al atravesar el disco actuador

3.3. Equilibrio de fuerzas en vuelo estacionario
3.3.1. Condición de hover

El vuelo estacionario se produce cuando el dron permanece suspendido sin aceleración vertical. En esta condición, el empuje total generado por los rotores equilibra exactamente el peso del sistema:

Ttotal = P

3.3.2. Requerimiento de empuje total

La teoría de cantidad de movimiento muestra que, para maximizar la eficiencia, el incremento de velocidad impartido al aire debe ser pequeño. Sin embargo, en aplicaciones reales se requiere un margen de empuje adicional para maniobras y control.

Por este motivo, en drones multirrotor se diseña el sistema de propulsión para que el empuje máximo total sea al menos el doble del peso del vehículo.

3.3.3. Distribución del empuje en multirrotores

En vuelo estacionario ideal, el empuje se distribuye uniformemente entre los N rotores:

Ti =

P
N

Durante maniobras, el controlador de vuelo modifica esta distribución para generar momentos alrededor de los ejes del dron.

3.4. Dinámica básica del multirrotor
3.4.1. Control de roll, pitch y yaw

El control del multirrotor se basa en la generación de momentos mediante diferencias de empuje entre los rotores. No se emplean superficies aerodinámicas móviles, sino variaciones en la velocidad angular de las hélices.

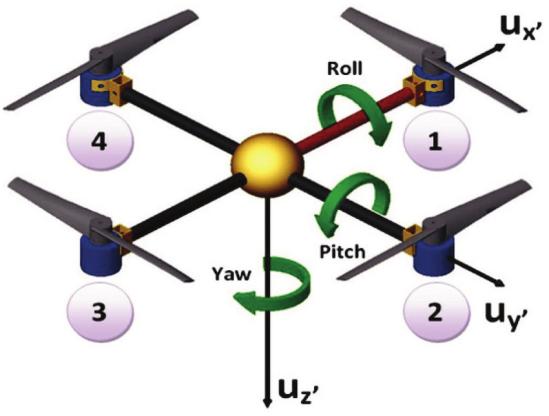
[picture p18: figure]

Referencia de | movimientos del dron
multirrotor.
3.4.2. Variación de velocidades angulares

La teoría de pala-elemento indica que el empuje de una hélice depende aproximadamente del cuadrado de su velocidad angular:

T ≃ α

2

Esto permite un control preciso del movimiento mediante pequeñas variaciones en la velocidad de los motores

3.4.3. Par reactivo y compensación

Cada hélice genera un par reactivo opuesto a su sentido de giro. Para evitar la rotación no deseada del dron sobre el eje vertical, los multirrotores utilizan hélices que giran en sentidos opuestos, compensando los torques individuales.

El control del yaw se logra modificando el balance de torque entre los grupos de hélices de giro horario y antihorario.

3.5. Empuje máximo y carga útil máxima
3.5.1. Condición mínima para despegar y hacer hover
Para condición de vuelo estacionario (hoover), la condición de equilibrio vertical es:

ΣT = P = m ∗ g
Donde:
ΣT = empuje total [N]
P = peso [N]
m = masa
g = gravedad

El dron en orden de marcha:

P = 2,15 kg ∗ 9,81 m/s2 = 21,1N

3.5.2. Modelo de empuje estático de hélice (aproximación) Estimamos el empuje estático con el coeficiente de empuje Ct:

T = Ct ∗ ρ ∗ n

2
∗ D

4
Donde:
T = empuje de una hélice [N]
Ct = coeficiente de empuje estático, dependiendo de la hélice varía entre 0,08 a 0,12 ρ = densidad del aire a nivel del mar = 1,125 kg/m3
D = diámetro de la hélice [M]
n = revoluciones por segundo (RPS)

Se conoce que:
- Diámetro de hélices es 8” → 0,2032 M
- Los motores giran 12000 RPM a 12V → n = 200 RPS

Calculamos:
ρ ∗ n

2 ∗ D

4 ≃ 83,54
Entonces:
T = Ct ∗ 83,54
3.5.3. Empuje máximo estimado (por motor y total)
El coeficiente Ct real corresponde a cada fabricante de hélices y es propio de generar diversas curvas dependiendo de la configuración hélice/motor elegidos.

Para la combinación de motor y hélice del dron, un valor realista es Ct = 0,1:
- Empuje por motor: 0,85 kgf
- Empuje total del dron: 5,11 kgf
3.5.4. Carga útil máxima (a empuje máximo)
En condiciones ideales, sin pérdidas ni factores externos:

Carga máxima = (ΣT) − P dron = 5,11 kg − 2,15 kg = 2,96 kg

La carga máxima teórica que puede transportar el dron es de 2,96 kg.

Esto en situaciones reales depende de la carga de la batería y de condiciones climáticas, sumando que no es recomendable volar a carga máxima debido a que no deja resto para maniobras imprevistas, lo que puede ocasionar accidentes.

Es buena práctica aplicar un coeficiente de seguridad para situaciones reales de 2 por lo menos, dejando la carga real operable en el rango de 1,5 kg.

### 4. Arquitectura física del dron desarrollado

La arquitectura física del sistema fue definida priorizando la estabilidad en vuelo, la modularidad, la facilidad de mantenimiento y la integración de sensores y actuadores adicionales.

4.1. Configuración general del prototipo

El prototipo se basa en una configuración multirrotor de seis motores (hexacóptero), seleccionada por su mayor capacidad de carga, redundancia y estabilidad frente a fallas parciales, en comparación con configuraciones de cuatro rotores.

La configuración general incluye:

- Estructura central portante (chasis)
- Brazos radiales con motores brushless en los extremos
- Sistema de propulsión compuesto por motores, hélices y ESC
- Sistema de control de vuelo
- Sistema de distribución de alimentación
- Sensores de navegación y detección
- Sistema mecánico de gripper para liberación de carga
- Cámaras montadas sobre base antivibratoria
4.2. Disposición de componentes

La disposición de los componentes fue seleccionada con el objetivo de minimizar interferencias mecánicas, eléctricas y electromagnéticas, así como de optimizar el balance del vehículo frente a las oscilaciones propias del movimiento del dron.

De forma general:

- Motores y hélices se ubican en los extremos de los brazos, generando un brazo de palanca adecuado para el control de actitud.
- ESC se montan próximos a cada motor, reduciendo la longitud de los cables de potencia y las pérdidas por efecto Joule.
- La batería se posiciona en medio del centro geométrico del chasis, debido a que es el elemento más pesado del dron y no debe generar tendencias al desbalance.
- Controlador de vuelo (Pixhawk) se monta sobre el eje central del dron, para que el sensado del acelerómetro y giróscopo sea correcto.

- Las cámaras se colocan en la parte inferior del dron, montadas en una base antivibratoria. Se orientan hacia abajo, para poder realizar capturas de elementos a nivel del suelo.
- El gripper se monta en una posición central inferior, alineado con el eje vertical del dron para evitar momentos indeseados durante la liberación de carga.

La disposición responde a criterios funcionales y dinámicos, buscando que las fuerzas y momentos generados durante el vuelo no introduzcan comportamientos no deseados.

4.3. Centro de masa y balanceo

El centro de masa del dron constituye un parámetro crítico para la estabilidad y el desempeño del sistema de control.

En el prototipo desarrollado, se buscó que el centro de masa coincida lo más posible con el centro geométrico del chasis, y se encuentre alineado con el eje vertical que pasa por el controlador de vuelo.

Para lograrlo, se aplicaron los siguientes criterios:

- Ubicación central de la batería, como componente de mayor masa.
- Simetría en la distribución de motores, brazos y ESC.
- Montaje alineado del gripper y de las cámaras.
- Posibilidad de ajuste longitudinal de la batería para correcciones finas.

Un centro de masa correctamente ubicado reduce:

- El esfuerzo de control requerido por los motores.
- El acoplamiento indeseado entre los ejes de roll, pitch y yaw.
- Las | oscilaciones | durante | vuelo | estacionario | y | maniobras | lentas.
4.4. Distribución estructural del chasis

El chasis del dron cumple simultáneamente funciones estructurales y de integración de sistemas.

Su diseño se basa en una estructura central rígida, de la cual parten los brazos que soportan los motores.

Las principales características de la distribución estructural son:

- Brazos radiales diseñados para soportar esfuerzos de flexión y torsión generados por el empuje de los motores.
- Cuerpo central donde se introducen los brazos y se realiza el montaje del controlador de vuelo.
- Base que se fija al cuerpo central, la misma alberga a la batería en posición central, es soporte de las patas y es donde se colocan los soportes de placas.
- Soportes de placas destinados a ubicar la Raspberry Pi y la placa con el ESP32 y el módulo LoRa. A su vez en los extremos se atornilla el soporte de cámaras y gripper.
- Soporte de gripper y base antivibratoria de cámaras (sobre la cual luego van fijadas las mismas).

La estructura fue concebida para ser liviana pero rígida, priorizando una buena relación resistencia–peso, fundamental para maximizar la autonomía del sistema.

### 5. Selección del sistema de propulsión

El sistema de propulsión constituye el subsistema central del dron, ya que es el encargado de generar el empuje necesario para el vuelo, permitir el control de la actitud y sostener la carga útil del vehículo.
Su selección se realizó considerando los requerimientos de empuje total, eficiencia energética, confiabilidad y compatibilidad con la arquitectura general del prototipo.
5.1. Motores brushless
5.1.1. Principio de funcionamiento

Los motores brushless de corriente continua (BLDC) utilizados en drones son máquinas eléctricas síncronas de imanes permanentes, en las cuales el rotor contiene imanes y el estator está compuesto por bobinados trifásicos.

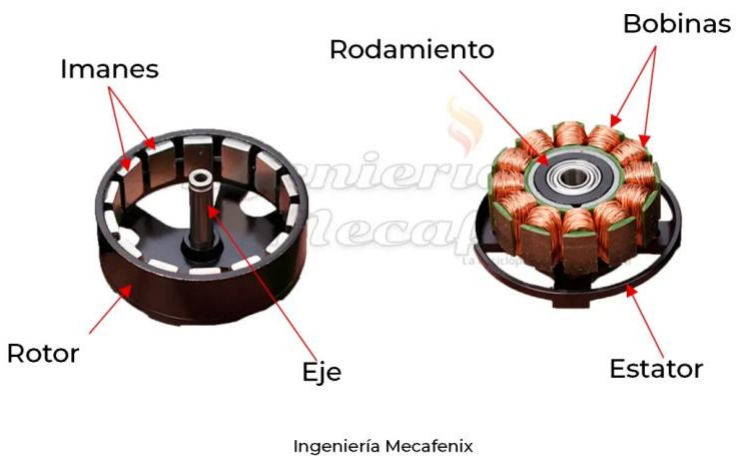
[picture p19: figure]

Componentes motor brushless

A diferencia de los motores con escobillas, la conmutación de corriente no se realiza de forma mecánica sino electrónicamente mediante un ESC, lo que permite:

- Mayor eficiencia
- Mayor vida útil
- Mejor control de velocidad
- Reducción del mantenimiento

El par generado por el motor produce la rotación de la hélice, transformando energía eléctrica en energía mecánica y, posteriormente, en energía cinética del flujo de aire.

5.1.2. Parámetro KV y su significado

El parámetro KV de un motor brushless indica la velocidad angular que el motor alcanza por cada volt aplicado en vacío:

KV =

RPM
Volt

Un motor con mayor KV gira a más revoluciones por voltio, mientras que uno con menor KV gira más lentamente pero es capaz de mover hélices de mayor diámetro y paso.

KV bajo → hélices grandes, mayor empuje, mejor eficiencia

KV alto → hélices pequeñas, mayor velocidad, menor eficiencia en hover

La selección del KV debe realizarse considerando el voltaje de la batería y el tipo de hélice a utilizar.

5.1.3. Criterios de selección de motores

Los principales criterios utilizados para la selección de los motores del prototipo fueron:

- Empuje máximo por motor, suficiente para sostener el peso del dron con margen.
- Compatibilidad con hélices de gran diámetro, favoreciendo la eficiencia.
- Corriente nominal adecuada, para no exceder las capacidades del ESC.
- Relación empuje–peso favorable, reduciendo masa total.
- Disponibilidad comercial, considerando el contexto de prototipado y las restricciones temporales de la cursada.

A nivel de diseño, se buscó que el empuje máximo total del sistema sea al menos el doble del peso total del dron, asegurando capacidad de maniobra y estabilidad.

5.1.4. Motores utilizados en el prototipo

El prototipo utiliza seis motores brushless modelo 2816, montados en configuración hexacóptero.
Este tipo de motor presenta:
- Tamaño adecuado para hélices de 8 pulgadas
- Buen compromiso entre par y velocidad

- Capacidad de generar empuje suficiente con tensiones de 3S (11,1V - 12,6V)
- Uso extendido en drones de tamaño medio

La elección de seis motores aporta redundancia y una mayor capacidad de carga respecto a configuraciones de cuatro rotores.

5.2. Controladores electrónicos de velocidad (ESC)
5.2.1. Función del ESC

El ESC (Electronic Speed Controller) es el encargado de convertir la tensión continua de la batería en señales trifásicas, controlando la velocidad del motor mediante modulación PWM.

Permiten ajustar con precisión la velocidad de cada motor para controlar la actitud del dron.

5.2.2. Corriente nominal y margen de seguridad

La corriente nominal del ESC debe ser superior a la corriente máxima esperada del motor bajo carga.

Como criterio de diseño, se adopta un margen de seguridad del 20 al 30%, tal que:

I ESC ≥ 1,3 ∗ I motor

Este margen reduce el riesgo de sobrecalentamiento y aumenta la confiabilidad del sistema durante maniobras exigentes.

5.2.3. Compatibilidad con motores y batería

La compatibilidad entre ESC, motor y batería se evaluó considerando:

- Tensión nominal de operación (3S)
- Corriente máxima admisible
- Frecuencia de respuesta
- Soporte para protocolo estándar de utilizado por el controlador de vuelo
5.2.4. ESC utilizados en el prototipo

En el prototipo se emplearon ESC de 30 A, uno por cada motor.

5.3. Hélices
5.3.1. Diámetro y paso

Las hélices se caracterizan principalmente por:

- Diámetro: determina el volumen de aire acelerado
- Paso: distancia teórica que avanzaría la hélice en una rotación completa

Hélices de mayor diámetro desplazan una mayor masa de aire a menor velocidad, lo que resulta más eficiente para vuelo estacionario.

5.3.2. Influencia en empuje y consumo

Según la teoría de cantidad de movimiento, es más eficiente generar empuje acelerando una gran masa de aire a baja velocidad que una pequeña masa a alta velocidad.

En consecuencia:

Hélices grandes → mayor empuje, menor consumo en hover

Hélices pequeñas → mayor consumo para igual empuje

La elección de hélice impacta directamente en la autonomía del dron.

5.3.3. Hélices de giro horario y antihorario

Cada hélice genera un par reactivo opuesto a su sentido de giro.

Para compensar este efecto, el dron utiliza hélices de giro horario (CW) y de giro antihorario (CCW), distribuidas alternadamente, permitiendo el equilibrio de torques y el control del yaw.

Si se colocaran todas las hélices iguales, los pares no se anularían y el dron giraría sobre su eje.

5.3.4. Hélices seleccionadas y justificación

El prototipo utiliza hélices 8×4,5 pulgadas, alternando de giro horario para motores impares y giro antihorario para los pares.

Esta selección se justifica por:

- Compatibilidad con motores 2816
- Buen compromiso entre empuje y consumo
- Disponibilidad comercial
- Adecuadas para tensiones de 3S

El conjunto motor–hélice permite generar el empuje necesario para el vuelo estacionario con un margen adecuado para maniobras.

### 6. Sistema de alimentación eléctrica

El sistema de alimentación eléctrica del dron es el encargado de suministrar la energía necesaria para el correcto funcionamiento de todos los subsistemas.
Su correcta selección impacta directamente en la autonomía, la capacidad de carga, la seguridad y la confiabilidad del sistema.

En un dron multirrotor, la batería constituye uno de los componentes de mayor masa, por lo que su elección representa un compromiso entre energía disponible y peso total del vehículo.

6.1. Tipos de baterías para drones
6.1.1. LiPo

Las baterías de polímero de litio (LiPo) son ampliamente utilizadas en drones debido a su elevada densidad de potencia, lo que les permite entregar corrientes muy altas en períodos cortos.

Sus principales características son:

- Alta tasa de descarga (C elevado), capacidad de suministrar grandes corrientes instantáneas
- Formato plano y liviano
- Uso extendido en aplicaciones RC y UAV

Como desventajas, presentan:

- Mayor sensibilidad a sobrecargas y descargas profundas
- Requerimientos estrictos de carga y balanceo
- Vida útil reducida si no se operan correctamente
6.1.2. Li-ion

Las baterías de ion de litio (Li-ion), como las celdas 18650 o 21700, se caracterizan por una mayor densidad energética, aunque con una menor capacidad de entrega de corriente en comparación con las LiPo.

Sus principales ventajas son:

- Mayor energía por unidad de masa
- Mayor vida útil
- Mejor estabilidad térmica

Sin embargo, presentan limitaciones importantes en drones multirrotor:

- Tasa de descarga más baja
- Menor capacidad para responder a picos de corriente
- Se debe colocar una configuración en paralelo para lograr corrientes de descarga comparables a las de una celda LiPo individual.

Por este motivo, su uso es más común en drones de largo alcance o configuraciones optimizadas para vuelo eficiente.

6.2. Parámetros eléctricos
6.2.1. Tensión nominal (S)

La tensión nominal de una batería se expresa mediante la cantidad de celdas conectadas en serie, indicadas como S.

Cada celda de litio presenta una tensión nominal aproximada de 3,7 V. A plena carga, 4,2 V.

Por ejemplo:

3S → 11,1 V nominal / 12,6 V a plena carga

4S → 14,8 V nominal / 16,8 V a plena carga

La tensión seleccionada debe ser compatible con los motores, ESC y electrónica del dron.

6.2.2. Capacidad (mAh)

La capacidad de la batería indica la cantidad de carga eléctrica que puede suministrar y se expresa en miliamperios-hora (mAh).

Una mayor capacidad permite mayor autonomía, pero también implica un aumento de masa, lo que incrementa el consumo y puede contrarrestar el beneficio energético.

6.2.3. Tasa de descarga C

La tasa de descarga C indica la corriente máxima que la batería puede suministrar de forma segura, y se define como:
Imax = C ∗ Capacidad

Por ejemplo, la batería utilizada de 5000 mAh con una tasa de 60C puede entregar

Imax = 60 ∗ 5A = 300A

6.3. Análisis de consumo y autonomía
6.3.1. Consumo estimado por motor

El consumo de cada motor depende del empuje requerido, la hélice utilizada y la tensión de alimentación.

En vuelo estacionario, cada motor genera aproximadamente:

Ti =

P
N

donde N es la cantidad de motores.

En esta condición, el consumo es significativamente menor al consumo máximo nominal del motor. Debido a que los movimientos del dron son considerados suaves, nos acercamos más a este consumo ideal que al máximo.

6.3.2. Consumo total del sistema

El consumo total del dron se obtiene de la suma de:

- Consumo de motores
- Consumo de controladora
- Consumo de microprocesadores
- Consumo de cámaras
- Consumo servo gripper

En la práctica el consumo de los motores es superlativamente mayor al resto de los componentes.

6.3.3. Autonomía teórica y práctica

La autonomía teórica la podemos calcular como:

t =

Capacidad útil de batería
I promedio

Sin embargo en situaciones reales no es posible utilizar el 100% de la capacidad de la batería, existen pérdidas eléctricas y aerodinámicas, se realizan maniobras que aumentan el consumo y otras situaciones, lo que nos lleva a asumir que la autonomía práctica puede ser del 80% de la calculada.

6.4. Batería utilizada en el prototipo
6.4.1. Justificación de elección - cálculo de tiempo de vuelo estimado

El prototipo utiliza una batería LiPo 3S de 45000 mAh con tasa de descarga 60C.

Para no sobre descargar y arruinar la batería suponemos un 80% de capacidad:

Cap usable = 0,8 ∗ 5Aℎ = 4Aℎ

Cálculo de corriente en hoover (sustentación en el lugar)

Empuje total requerido:

Ttotal ≃ m ∗ g = 2,15 kg ∗ 9,81 m/s2 ≃ 21,1N

Empuje por motor (6 motores):

Tmotor ≃

21,1 N
6

≃ 3,52N ≃ 0,36 kgf

Como no tenemos la curva en banco de empuje del motor con hélice (empuje vs corriente consumida), vamos a suponer un consumo razonable de 30A + 3A de electrónica.

Suponiendo una distancia media de navegación entre waypoints de 10 metros, el dron recorre en:

t nav =

10 m
Vel [s]

El tiempo en hoover:

t ℎoover = 3 segundos

Lógicamente el consumo de corriente es algo mayor durante la navegación, usamos:

Inav ≈ 1,15 ∗ Iℎoov

Consumo por tramo en Ah:

Aℎ tramo =

Inav ∗ Tnav
3600s

+

Iℎoov ∗ Tℎoov
3600s

El momento de despegue y aterrizaje tambien suponen consumos considerables, por lo que descontamos un 10% de la bateria en cuestion de reserva:

Aℎ efectiva para tramos = 0,9 ∗ 4Aℎ = 3,6 Aℎ

Máxima cantidad de waypoints posibles:

- Si hay N waypoints hay N-1 tramos
- Hay N hoovers (uno por wp)

Consumo total:

Aℎ(N) =

Inav ∗ Tnav ∗ (N − 1)
3600s

+

Iℎoover ∗ Tℎoover ∗ N
3600s

+ Aℎ reserva

Se busca el máximo N tal que Aℎ ≤ 4Aℎ

Navegando a velocidad de 5 m/s → N ≈ 74 waypoints

Navegando a velocidad de 3 m/s → N ≈ 58 waypoints

Tiempo de vuelo asociado

N waypoints:

t total ≈ N ∗ 3s + (N − 1) ∗

10m
v

Navegando a velocidad de 5 m/s → N ≈ 74 waypoints → 368 segundos ≈ 6,1 m

Navegando a velocidad de 3 m/s → N ≈ 58 waypoints → 364 segundos ≈ 6,1 m

La variabilidad de estos cálculos puede ser muy amplia debido a que el dron puede verse afectado por condiciones climatológicas que dificulten el vuelo, o variaciones en la misión tales como el espaciado entre waypoints, que para el fin del cálculo se establece en 10 metros. La carga del paquete del gripper también afectará en gran porcentaje a la autonomía.

6.4.2. Ventajas y limitaciones

Ventajas:

- Alta capacidad de descarga
- Respuesta rápida ante cambios de carga
- Simplicidad de integración

Limitaciones:

- Autonomía limitada en comparación con soluciones Li-ion
- Requiere cuidados durante carga, almacenamiento y operación
- Degradación acelerada si se exceden los límites operativos

Estas limitaciones son aceptables en el contexto de un prototipo experimental, donde se prioriza la confiabilidad del empuje y la capacidad de maniobra.

### 7. Métodos de manufactura del prototipo

7.1. Enfoque de prototipado rápido

La fabricación del prototipo funcional se basó en el ciclo diseño-fabricación-prueba pudiendo evaluar situaciones reales antes de hacer un diseño definitivo. Ajustes de integración de las partes y para facilitar el mantenimiento fueron hechos sobre la marcha, tales como huecos en el cuerpo para poder conectar cable USB para cargar el programa al ESP32, o bien un sistema de sujeción rápida para la batería.

7.1.1. Iteración y validación

El proceso seguido puede resumirse en las siguientes etapas:

1. Diseño inicial en CAD de los componentes estructurales.
2. Fabricación rápida (impresión 3D).
3. Montaje y pruebas funcionales (ajuste de posiciones de motores y electrónica, verificación de interferencias mecánicas).
4. Evaluación de rigidez y vibraciones.
5. Correcciones de diseño en función de los resultados obtenidos.
6. Nueva fabricación de las piezas modificadas.

Este ciclo se repitió hasta obtener piezas con la solidez y funcionalidad esperadas.

7.1.2. Ventajas frente a manufactura industrial

En comparación con métodos industriales tradicionales (mecanizado CNC, inyección, prfv), el prototipado rápido con el ciclo de iteración CAD - impresión 3D ofrece:

- Reducción significativa de costos iniciales.
- Menor tiempo entre iteraciones.
- Libertad geométrica para integrar electrónica y cableado.
- Facilidad para realizar modificaciones sin rehacer el conjunto completo.

En contraparte, no es un método fácilmente escalable, debido a la poca velocidad de producción de las piezas.

7.2. Fabricación del chasis
7.2.1. Diseño CAD

El chasis fue diseñado íntegramente mediante herramientas de diseño asistido por computadora (CAD), lo que permitió:

- Definir con precisión la geometría del dron.
- Integrar desde el inicio los puntos de fijación de motores, electrónica de control, batería, gripper y cámaras
- Evaluar el ensamblaje completo antes de la fabricación, tomando importante relevancia, debido a que poder analizar las interacciones entre todos los componentes permitió reducir los ciclos de iteración de prototipado.

El uso de CAD también facilitó la exportación directa de los modelos a formato compatible con impresión 3D, reduciendo errores de interpretación durante la manufactura.

7.2.2. Materiales seleccionados para la confección del prototipo

El dron está constituido íntegramente de impresión 3D y aluminio, logrando un excelente y apropiado balance entre peso y rigidez, sin estorbar la normal operativa del mismo.

Los seis brazos que sujetan a los motores y ESC fueron realizados en tubo cuadrado de aluminio 6061, en medida 12mm x 12 mm x 0,7 mm de espesor. Otorgan gran resistencia con poco volumen (respecto de una pieza de similares características mecánicas realizada en impresión 3D) lo que es crucial para no obstruir el flujo de aire creado por las hélices y perder rendimiento.

El resto del chasis del dron fue impreso íntegramente con filamento PETG ya que encontramos múltiples ventajas en el uso de este material:
- El costo es similar al del PLA
- Facilidad de impresión y adherencia a la cama - poco y nulo warping respecto a ABS
- Excelente capacidad mecánica y alta tenacidad
- Temperatura de fusión más alta que PLA, lo que permite trabajarlo con herramientas manuales para ajuste fino, y no tener que volver a reimprimir.
- Alta estabilidad química
- El PETG puede verse afectado por largos periodos de exposición UV, volviéndose quebradizo, pero como el prototipo no volará por periodos extendidos no es un ítem de gran relevancia.
Los parámetro elegidos para la impresión fueron:
- Tº hotend: 245ºC - la máxima recomendada por el fabricante del filamento, ayuda a conseguir una mejor adhesión entre capas aunque el acabado quede más brillosos
- Tº cama:70ºC
- 3 capas de pared, 3 capas de piso, 3 capas de techo - para poder reducir relleno

- Relleno: 20% tipo giroide - este tipo es el que mejor características mecánicas isotrópicas tiene
- Tolerancias dimensionales para ajuste deslizante
7.3. Elementos de fijación

La correcta selección de los elementos de fijación es fundamental para garantizar la integridad estructural del dron durante el vuelo y facilitar el mantenimiento.

7.3.1. Tornillería

Se eligió utilizar tornillería de 1/8 “ en todo el dron, para asegurar un armado sencillo.

Los mismos fueron utilizados para fijar motores a los brazos, los brazos al cuerpo, el cuerpo a la base y los soportes de placa.

Para fijar las patas a la base se cortaron dos tramos de varilla roscada de la misma medida, ya que fue imposible conseguir tornillos de tal largo.

7.3.2. Correas y sujetadores

La sujeción de la batería en su receptáculo se realizó utilizando una banda elástica sostenida entre dos salientes, con el fin de facilitar su reemplazo en campo.

La carga del gripper va sujeta con una correa ajustable, con el fin de que se adapte a cualquier geometría del elemento a transportar.

### 8. Ensambles mecánicos del dron

El correcto ensamblaje mecánico del dron es un aspecto fundamental para garantizar la integridad estructural, la confiabilidad durante el vuelo y la correcta operación de los sistemas electrónicos y de propulsión.

8.1. Ensamble general del chasis

El chasis del dron fue pensado como una estructura modular, permitiendo dividir el sistema en subensambles independientes, lo que facilitó tanto el montaje inicial como las tareas de mantenimiento y modificación posteriores.

8.1.1. Subensambles

El dron puede descomponerse en los siguientes sub ensambles mecánicos principales:

- Cuerpo central
- Brazos estructurales
- Soporte motor, motor, hélice, soporte hélice
- Base central
- Soportes de placas
- Soporte de gripper y base antivibratoria para cámaras
- Bloque de cámaras

Esta división permitió trabajar de manera independiente en cada conjunto y luego integrarlos en el ensamblaje final.

8.1.2. Orden de montaje

El orden de montaje adoptado fue definido para minimizar interferencias mecánicas y facilitar el acceso a tornillería y conexiones:
1. Montaje de motores a soportes y de soporte de hélices a eje de motor (x6)
2. Montaje de conjunto motor a extremo de brazo y montaje de ESC (x6)
3. Montaje de brazos a cuerpo central, utilizando sólo los tornillos pasantes externos, ya que los internos son requeridos para montar la base.
4. Montaje de base central a cuerpo utilizando los tornillos faltantes.
5. Montaje de soportes de placa y placa ESP32 y raspberry pi.
6. Montaje de power module y step down en los lados de la base.
7. Colocación del soporte de cámaras y gripper (con estos ya colocados) entre los soportes de placa, a los cuales cierra y da rigidez al conjunto.
8. Instalación de patas de aterrizaje.
9. Instalación de controladora pixhawk y sensores.
10. Enrutado y fijación de cables.

11.Colocación de hélices (último ítem, por seguridad).

8.2. Ensamble del sistema de propulsión

El montaje de este subsistema debe ser en extremo un ítem de alto cuidado debido a que está expuesto a vibraciones permanentes, además se debe asegurar la alineación y rigidez de contacto, ya que el control y sustentación del dron depende de ello.

8.2.1. Montaje de motores

Los motores se montan a los brazos utilizando los soportes metálicos que vienen incluidos en los kits de motores.

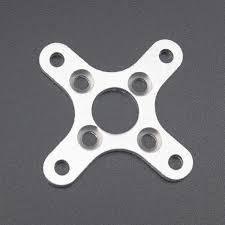
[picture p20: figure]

Estos se atornillan a la base del motor y luego se colocan tornillos pasantes en los extremos contra los brazos.

8.2.2. Fijación de hélices

La fijación de las hélices a los ejes de los motores brushless se realiza mediante acoples cónicos, los cuales al apretar la tuerca se aprietan contra el eje. Se colocan con rosca izquierda en aquellos de giro antihorario y de rosca derecha en aquellos de giro horario.

8.2.3. Ubicación de ESC

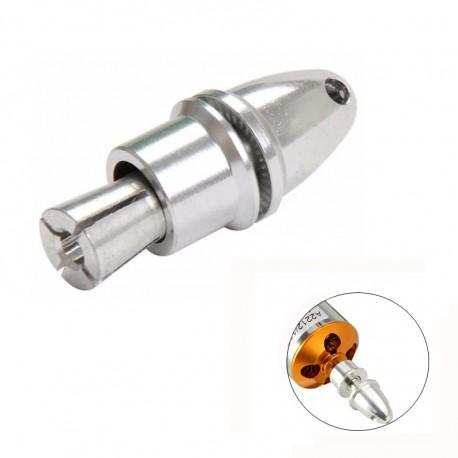
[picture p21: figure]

Los controladores ESC se colocan sobre los brazos, cercanos a los motores para reducir longitud de cables de potencia, minimizar pérdidas eléctricas y aprovechar que es una ubicación bien ventilada para ayudar a la disipación térmica.

La fijación se realizó firmemente mediante bridas plásticas (precintos).

8.3. Ensamble de electrónica

La ubicación de los componentes electrónicos se realizó con el fin de colocar sensores en una posición óptima para su funcionamiento y colocar placas electrónicas en sitios seguros y sin vibraciones, además de lo más alejado posible de motores.

8.3.1. Controladores

El controlador de vuelo Pixhawk fue montado en una posición central del chasis, próxima al centro de masa del dron, alineándolo con los ejes del dron debido a que el acelerómetro y giróscopo están integrados, favoreciendo a una mejor respuesta del sistema. Además la posición facilita las conexiones de ESC y demás conectores.

8.3.2. Sensores

El gps y magnetómetro fueron montados sobre un poste de unos 15 cm, debido a que son extremadamente sensibles a los campos electromagnéticos. Esto asegura su correcto funcionamiento y mediciones estables en el tiempo.

8.3.3. Cableado y gestión de vibraciones

El cableado se organizó de la forma más prolija posible, tratando de hacer cruces a 90º cuando dos cables se enciman y teniendo cuidado con la tensión mecánica en los conectores.

Los cables se fijaron mediante bridas plásticas (precintos) haciendo pequeños bucles donde pueden ocurrir vibraciones.

### 9. Diseño y construcción del gripper

El gripper constituye un subsistema mecánico auxiliar del dron, diseñado para permitir la sujeción y liberación controlada de una carga durante la misión.
Se buscó un diseño simple y específico para la tarea, donde sólo debe liberar la carga.
9.1. Función del gripper en la misión

La función principal es la de entregar un paquete de asistencia a una persona en situación de búsqueda y rescate, una vez detectada por los sensores.

Durante la misión, el gripper debe tener la carga sujeta firmemente mientras vuela, no inferir con el funcionamiento del dron ni desestabilizarlo al soltar la carga.

9.2. Requisitos mecánicos y funcionales

Ya teniendo en claro qué debe hacer el gripper se establecen una serie de requisitos:

- Capacidad de soportar el peso del paquete con cierto margen
- Resistencia a vibraciones y aceleraciones propias del vuelo
- Peso contenido y geometría compacta para no inferir con el chasis ni con las cámaras
- La liberación se realiza mediante una señal eléctrica
- Estado estable cerrado
- Consumo energético bajo
- Simplicidad de mantenimiento y reemplazo
9.3. Diseño del mecanismo

El gripper fue diseñado como un mecanismo de sujeción pasivo–activo, donde la carga se mantiene retenida mecánicamente y la liberación se realiza mediante un actuador simple.

9.3.1. Perno pasante

El elemento principal de sujeción es un perno pasante, el cual asegura la retención de la carga. El mismo atraviesa el soporte del gripper y el soporte de la correa de sujeción.

9.3.2. Correa de sujeción

Se eligió colocar una correa (fija en un punto y en otra solidaria al soporte que agarra el perno pasante) con la finalidad de dar mayor flexibilidad a la hora de colocar una carga.

La misma se compone de un lazo de velcro, ajustable entre sí.

9.3.3. Accionamiento por servo

El movimiento del perno pasante está ligado al accionamiento de un servo sg90, la conjunción de estos dos métodos nos permite utilizar un servo pequeño y de bajo consumo ya que la carga no yace sobre él, si no, sobre el perno creando una solicitud al corte sobre el mismo.

9.4. Proceso de construcción
9.4.1. Materiales

Los materiales utilizados fueron seleccionados priorizando bajo peso y facilidad de fabricación:

- Piezas estructurales: impresión 3D con los mismos criterios que el resto del cuerpo.
- Perno pasante: tornillo ⅛ “ cortado al largo justo para permitir liberación y soporte.
- Correa: velcro polyester de alta resistencia.
- Accionamiento: servo sg90 9 gramos.
9.4.2. Ensamble final

El ensamblaje del gripper se realizó siguiendo el orden:
1. Colocación del servo con la leva simple en la base (servo en 0º)
2. Se instala el tornillo en la pieza móvil interface y se coloca el conjunto en la corredera
3. Se mueve el servo 35º, donde engancha con el receptáculo de la pieza móvil con el tornillo
4. Se fija el tope guía con pegamento
5. Se instala la correa en el soporte fijo
6. Se cierra el servo (105º) trabando el gancho de la correa
7. La correa se puede enlazar en el gancho móvil y asegurar la carga

Montaje del gripper (sin correa ni carga):

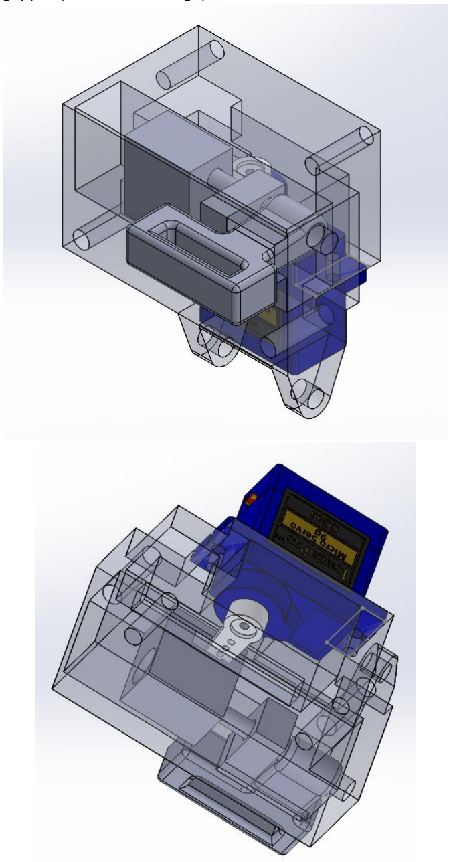
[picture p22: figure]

### 10. Sistema de montaje de cámaras

El sistema de montaje de cámaras cumple un rol crítico en el desempeño del dron, ya que de él depende la calidad de la información visual y térmica adquirida durante la misión.
Un montaje inadecuado puede introducir vibraciones o desalineaciones que degradan significativamente los resultados del procesamiento de imágenes.

Por este motivo, el diseño del soporte de cámaras fue realizado considerando criterios de estabilidad, aislamiento vibratorio y correcta integración estructural con el chasis del dron.

10.1. Requisitos de estabilidad y aislamiento

A partir de la función de las cámaras durante la misión (detección y análisis) se establecieron los requerimientos:

- Mantener orientación estable
- Reducir transmisión de vibraciones provenientes del sistema de propulsión
- Evitar movimiento relativo entre cámaras y dron
- Permitir acceso para conexión y desconexión de las mismas, para no entorpecer el desarrollo del prototipo

La cámara térmica se ve especialmente afectada por vibraciones, por lo que la confección correcta del módulo es de suma importancia.

10.2. Fuentes de vibración en el dron

Diversos motivos pueden desencadenar en la generación de fuentes no deseadas de vibraciones:
- Desbalanceos dinámicos en los motores brushless
- Hélices con pequeñas imperfecciones que puedan generar desbalanceos
- Variación de empuje de los motores, propios del movimiento del dron
- Flujo de aire sobre el dron
10.3. Diseño de la base antivibración

Para mitigar los efectos de las múltiples fuentes de vibración que pueden presentarse en el dron se escogió utilizar una base antivibración para montar el módulo de cámaras al cuerpo del dron.
El desacople vibratorio se realiza con la incorporación de elementos elásticos, los cuales actúan como filtro mecánico entre la base y el chasis, reduciendo la amplitud de las vibraciones transmitidas.

10.3.2. Geometría del soporte

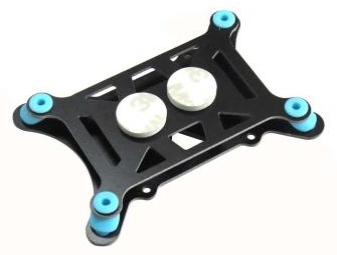
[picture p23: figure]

La geometría del soporte fue resuelta para albergar ambas cámaras y dotarlas de algo de peso en su conjunto, con la finalidad de conseguir una mejor respuesta de la base antivibración.

10.3.3. Ubicación en el chasis

Las cámaras se ubican entre las patas del dron, lo más cercanas posible al centro de masa para reducir desbalanceos dinámicos.

10.4. Ensamble y fijación de cámaras

Ambas cámaras fueron fijadas en conjunto mediante un soporte confeccionado en impresión 3D, en concordancia con el resto del prototipo.

### 11. Planos y documentación técnica

La correcta documentación técnica del prototipo desarrollado resulta fundamental para garantizar la reproducibilidad, mantenimiento, análisis estructural y posibles mejoras futuras del sistema. En este capítulo se presentan los planos y esquemas correspondientes a los principales subconjuntos mecánicos del dron, elaborados a partir del diseño CAD utilizado durante el proceso de desarrollo.

Dado que se trata de un prototipo experimental, los planos se enfocan en definir geometrías funcionales, interfaces mecánicas, dimensiones críticas y criterios de montaje, sin llegar al nivel de tolerancias propias de manufactura industrial en serie.

Los planos se encuentran en el anexo de este informe, únicamente serán mencionados

11.1. Planos del chasis
- PL-01 Cuerpo dron
- PL-02 Base dron
- PL-03 Soporte placas
- PL-04 Base camaras gripper
- PL-06 base antena lora
- PL-12 Ensamble dron
11.2. Planos del gripper
- PL-05 cuero gripper
- PL-11 ENSAMBLE GRIPPER
11.3. Planos del soporte de cámaras
- PL-09 Soporte cámaras
- PL-10 Tapa soporte camaras

### 12. Resultados y validación experimental

Con el objetivo de verificar el correcto funcionamiento del dron desarrollado, se realizaron una serie de pruebas experimentales destinadas a validar el comportamiento estructural, la capacidad de vuelo y la estabilidad del sistema durante la operación.

Las pruebas se llevaron a cabo de forma progresiva, comenzando por ensayos en tierra y culminando con vuelos controlados, permitiendo identificar y corregir posibles inconvenientes antes de avanzar a etapas más exigentes.

12.1. Pruebas estructurales

Se realizaron pruebas en banco, sin las hélices instaladas, para verificar que no existan vibraciones indeseadas en todo el rango de revoluciones de los motores.
Se tomaron diversas capturas con las cámaras verificando la nitidez de la imagen térmica y la imagen RGB.

También se constató la rigidez del conjunto y fijaciones.

Se verificó el correcto funcionamiento del gripper portapaquetes.

12.2. Pruebas de vuelo

Antes de comenzar las pruebas de vuelo se realizaron pruebas sin hélices, verificando que el sistema reconociera los waypoints y la navegación se ejecutaba de forma correcta.

Seguido a esto, se realizó una prueba corta de despegue, estabilización y aterrizaje, chequeando que los comandos de emergencia respondan satisfactoriamente.

Luego procedimos a realizar vuelos lineales, es decir, sin cumplir un patrón de análisis en un polígono, realizando análisis con las cámaras y chequeando el comportamiento de las opciones continuar misión o volver tras una detección.

Por último, realizamos la prueba del sistema en estado final, realizando el patrón de barrido en el polígono, revisando que se detenga en cada waypoint y que realice las detecciones pertinentes, accionando el gripper cuando sea necesario.

### 13. Conclusiones

El desarrollo del presente proyecto permitió diseñar, construir e implementar un dron multirotor funcional, orientado a tareas de búsqueda y análisis mediante sensores. A lo largo del trabajo se integraron criterios mecánicos, eléctricos y de control, los cuales validaron experimentalmente las decisiones adoptadas.

13.1. Evaluación del diseño físico

El diseño físico del dron cumplió de manera satisfactoria con los objetivos planteados para un prototipo experimental.

Entre los principales aspectos positivos se destacan:

- Estructura mecánica adecuada, con rigidez suficiente para soportar las cargas dinámicas del vuelo.
- Correcta distribución de componentes, logrando un centro de masa equilibrado y un comportamiento dinámicamente estable.
- Integración efectiva del sistema de propulsión, con motores, hélices y ESC correctamente dimensionados.
- Sistema de gripper funcional, que permite la liberación exacta del paquete transportado.
- Montaje con base antivibratoria de cámaras, que mejora la estabilidad de las imágenes y la calidad de los datos adquiridos.
13.2. Limitaciones del prototipo

Como todo prototipo experimental, el dron presenta una serie de limitaciones que fueron identificadas durante el desarrollo y las pruebas:

- Autonomía limitada, principalmente condicionada por la capacidad de la batería y el peso total del sistema.
- Materiales de fabricación, la impresión 3D es adecuada para validar un prototipo pero no está optimizada para uso intensivo o de largo plazo.
- Sensibilidad a vibraciones, propia de drones multirrotor, aunque mitigada mediante diseño mecánico.
- Dependencia de condiciones ambientales, como viento, que afectan estabilidad y consumo energético.
- Capacidad de carga reducida, acorde a un prototipo con tamaño y potencia reducidos
- Incapacidad de sortear objetos o volar en interiores, debido a la falta de sensor lidar

Estas limitaciones no invalidan el funcionamiento del sistema, sino que delimitan su alcance dentro del contexto experimental.

13.3. Posibles mejoras futuras

A partir de las limitaciones observadas podemos concluir en diversas líneas de mejoras futuras:
- Utilización de aluminio (similar a los brazos) para las patas, dotandolas de mayor largo y resistencia a impactos.
- Fabricación de cuerpo y base en plástico inyectado o algún material de ingeniería compuesto.
- Mejorar la autonomía, utilizando baterías más grandes u otro tipo, con mayor densidad energética.
- Optimización de diseño aerodinámico con la fabricación de una carcasa ya que los componentes están expuestos.
- Ampliar capacidades colocando más sensores, como un lidar para vuelo entre obstáculos a baja altura o vuelo en interiores.
- Fabricacion de electronica propietaria que confluya todos los sistemas informáticos en un único microprocesador, en fin de la eficiencia energética y la confiabilidad de vuelo.

### 14. Normativa UAV en Argentina

El uso y operación de vehículos aéreos no tripulados (UAV), también denominados VANT (Vehículos Aéreos No Tripulados), en la República Argentina se encuentra regulado por la Administración Nacional de Aviación Civil (ANAC). La normativa vigente establece los requisitos técnicos, operativos y de seguridad aplicables según el tipo de operación y el peso de la aeronave.

14.1. Autoridad regulatoria

Administración Nacional de Aviación Civil (ANAC), organismo dependiente del Ministerio de Transporte de la Nación, responsable de regular, fiscalizar y controlar la actividad aeronáutica civil en Argentina.

14.2. Marco normativo principal

La normativa aplicable a UAV se encuentra incorporada en:

Regulaciones Argentinas de Aviación Civil (RAAC), Parte 101 – Vehículos Aéreos No Tripulados (VANT)

Esta sección establece las condiciones bajo las cuales pueden operar los drones en el espacio aéreo argentino.

14.3. Clasificación de UAV según normativa argentina

La RAAC Parte 101 clasifica los UAV principalmente en función de:

- Peso máximo de despegue
- Tipo de operación
- Finalidad recreativa o profesional

De manera general:

- Uso recreativo / aeromodelismo
- Uso profesional o experimental
- Operaciones especiales (BVLOS, nocturnas, zonas controladas)

El prototipo desarrollado en este proyecto se enmarca dentro de la categoría de UAV experimental/prototipo, con fines académicos y de investigación.

14.4. Reglas operativas generales

Entre las principales restricciones establecidas por la normativa se destacan:
- Operación dentro del alcance visual del piloto (VLOS).

- Altura máxima limitada sobre el nivel del terreno.
- Prohibición de vuelo sobre:
- Concentraciones de personas
- Infraestructura crítica
- Aeródromos sin autorización
- Distancia mínima respecto de personas, vehículos y edificaciones.
- Prohibición de operaciones autónomas sin supervisión humana directa, salvo autorización expresa.
14.5. Requisitos técnicos y de seguridad

La normativa exige que los UAV cuenten con:

- Identificación del operador.
- Sistemas de control confiables.
- Procedimientos de emergencia (failsafe).
- Condiciones estructurales seguras.
- Sistemas de energía adecuados y protegidos.

En el caso del prototipo desarrollado, se contemplan:

- Control de vuelo mediante piloto automático.
- Retorno automático ante eventos críticos.
- Monitoreo de batería y estados del sistema.
- Ensayos controlados en entornos no poblados.
14.6. Alcance normativo del proyecto

El presente proyecto tiene un alcance académico y experimental, no orientado a operación comercial ni a certificación aeronáutica. No obstante, el diseño y las pruebas se realizaron considerando las buenas prácticas y los principios de seguridad establecidos por la normativa ANAC vigente.

Esto permite que el prototipo sea técnicamente escalable a futuras etapas de validación normativa si se requiriera.

### 15. Referencias bibliográficas

15.1 Aerodinámica básica

Anderson, J. D., Fundamentals of Aerodynamics., McGraw-Hill Education, 6th Edition, 2016.

Leishman, J. G., Principles of Helicopter Aerodynamics., Cambridge University Press, 2nd Edition, 2006.

Apuntes de cátedra – Teoría de hélices y propulsión aérea. UNLP, Ingeniería aeronáutica

15.2 Motores brushless

Hughes, A., & Drury, B., Electric Motors and Drives: Fundamentals, Types and Applications., Elsevier, 4th Edition, 2013.

SimonK / BLHeli Documentation, ESC Firmware and Motor Control Theory for Multirotors.

15.4 Normativa UAV

Administración Nacional de Aviación Civil (ANAC)., Regulaciones Argentinas de Aviación Civil (RAAC), Parte 101 – Vehículos Aéreos No Tripulados.

ANAC – Publicaciones y circulares informativas sobre VANT/UAV.

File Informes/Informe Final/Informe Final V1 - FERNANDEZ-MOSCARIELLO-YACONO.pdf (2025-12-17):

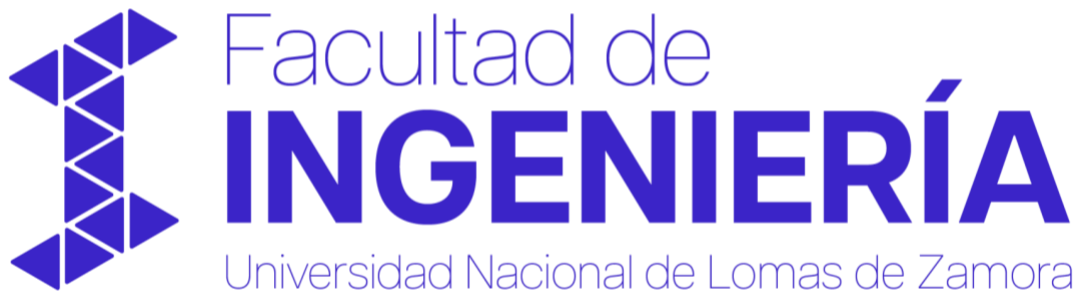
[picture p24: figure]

# PROYECTO EN INGENIERÍA MECATRÓNICA

# Dron autopilotado con detección de fuego y personas mediante procesamiento IA de cámaras

## Integrantes:

- FERNANDEZ MALENOTTI, Ignacio | DNI: 42.043.463
- MOSCARIELLO, Christian | DNI: 37.053.307
- YACONO, Emiliano | DNI: 34.485.253

## Docentes:

## - Ing. Blanca, Ezequiel - Ing. Lukaszewickz, Cristian - Ing. Szombach, Juan

Facultad de Ingeniería
Universidad Nacional de Lomas de Zamora

Contenido

5.2.1 Ventaja del prototipo: IA entrenada específicamente para incendios y personas. 8

Facultad de Ingeniería
Universidad Nacional de Lomas de Zamora

Facultad de Ingeniería
Universidad Nacional de Lomas de Zamora

Facultad de Ingeniería
Universidad Nacional de Lomas de Zamora

### 1. Título del Proyecto

Dron Autónomo para Detección de Incendios y Rescate de Personas

### 2. Introducción

Durante los meses de verano, diferentes áreas naturales —como parques nacionales, reservas ecológicas y zonas de montaña— se ven afectadas por dos problemáticas críticas y de creciente relevancia: la aparición de focos de incendio y el extravío de personas en entornos de difícil acceso. La vegetación seca y las altas temperaturas favorecen la rápida propagación del fuego, mientras que la amplitud del terreno y la escasez de personal dificultan las tareas de búsqueda, control y patrullaje terrestre.

La detección tardía de un foco ígneo o la demora en localizar a una persona extraviada incrementan significativamente el riesgo para la vida humana y el impacto ambiental. Si bien los helicópteros representan una herramienta efectiva para tareas de vigilancia aérea, su uso implica costos operativos elevados, limitaciones en disponibilidad y una cobertura espacial acotada, lo que restringe su empleo de manera continua o preventiva.

Ante este escenario, surge la necesidad de explorar alternativas tecnológicas más accesibles, flexibles y autónomas, capaces de brindar una respuesta temprana y asistir a equipos de emergencia en situaciones donde cada minuto resulta determinante.

### 3. Objetivo y Propuesta del Proyecto

El presente proyecto busca desarrollar un prototipo funcional de dron autónomo a escala, orientado a operaciones de monitoreo, detección temprana y apoyo logístico en contextos de incendio o búsqueda y rescate. La propuesta abarca las siguientes capacidades principales:

1. Detección visual y térmica de focos de incendio en etapas iniciales.
2. Localización de personas extraviadas mediante análisis de imágenes RGB e infrarrojas.
3. Transmisión de coordenadas geográficas precisas hacia una estación base para facilitar la intervención.
4. Transporte de pequeñas cargas, tales como elementos de supervivencia, primeros auxilios o materiales para iniciar la contención temprana de un incendio.

Facultad de Ingeniería
Universidad Nacional de Lomas de Zamora

El alcance del proyecto no busca reemplazar a sistemas profesionales de respuesta aérea, sino demostrar la viabilidad técnica de una plataforma autónoma liviana, versátil y de bajo costo, capaz de inspeccionar grandes superficies y asistir en tareas que actualmente requieren importantes recursos humanos y económicos.

### 4. Enfoque del Desarrollo

El desarrollo del proyecto se abordó desde una perspectiva integral de la ingeniería mecatrónica, combinando conocimientos y técnicas de diversas áreas para construir un prototipo funcional capaz de ejecutar tareas complejas de manera autónoma. El enfoque adoptado prioriza la modularidad, permitiendo diseñar, probar e integrar cada subsistema de forma independiente antes de su ensamblaje final.

En materia de percepción del entorno, se implementó un esquema de detección multimodal basado en cámaras RGB y sensores térmicos infrarrojos. Este sistema permite identificar focos de incendio y localizar personas tanto mediante análisis visual tradicional como a través de diferencias de temperatura en la escena. Para potenciar estas capacidades, se incorporan algoritmos de inteligencia artificial entrenados específicamente para las clases relevantes del proyecto (fuego y personas).

El procesamiento de datos se realizó mediante sistemas embebidos, combinando una Raspberry Pi 4 para tareas de visión por computadora y analítica, y una ESP32 encargada de comunicaciones y control de misión. La arquitectura se complementa con la controladora Pixhawk, responsable de la estabilización del dron y la ejecución del vuelo autónomo mediante GPS y el protocolo MAVLink.

En el ámbito de comunicaciones inalámbricas, se adoptó un módulo LoRa de largo alcance para transmitir eventos detectados, garantizando operación en entornos rurales o de baja infraestructura. Esta elección permitió validar la viabilidad de enviar información crítica aún bajo restricciones severas de ancho de banda.

Finalmente, la etapa de integración combinó navegación autónoma, percepción multimodal, procesamiento inteligente y transmisión de alertas en un único flujo de misión. El resultado es un sistema capaz de despegar, desplazarse entre waypoints, detenerse para analizar su entorno, detectar situaciones relevantes, reportarlas a una estación base y continuar su ruta de manera autónoma.

Este enfoque refleja la convergencia de mecánica, electrónica, software, telecomunicaciones e inteligencia artificial, consolidando un prototipo alineado con las tendencias actuales de automatización y apoyo tecnológico en operaciones de emergencia.

Facultad de Ingeniería
Universidad Nacional de Lomas de Zamora

### 5. Análisis del Mercado y Tecnologías Disponibles

En el mercado actual existe una oferta consolidada de vehículos aéreos no tripulados (UAVs) diseñados para tareas de vigilancia ambiental, detección temprana de incendios y operaciones de búsqueda y rescate. Fabricantes como DJI y Autel Robotics han desarrollado plataformas avanzadas —entre ellas el DJI Matrice 30T y el Autel EVO II Dual— equipadas con cámaras térmicas de alta resolución, sensores ópticos de largo alcance, inteligencia artificial embarcada y transmisión de video en tiempo real. Estas aeronaves se utilizan ampliamente en brigadas forestales, bomberos y equipos de emergencia debido a su capacidad para inspeccionar grandes superficies, operar en condiciones climáticas adversas y enviar información crítica a centros de control en cuestión de segundos.

A pesar de la diferencia en escala, prestaciones y costos, estos drones comparten varias funciones esenciales con el propósito central de este proyecto, entre ellas:

- Detección térmica de focos de calor, permitiendo identificar incendios en etapas tempranas.
- Registro visual de alta precisión, útil para tareas de reconocimiento del entorno y búsqueda de personas.
- Transmisión remota de información georreferenciada a una estación base operativa.
- Navegación autónoma o semiautónoma, asistida por GPS y sistemas de piloto automático.

Estas capacidades representan el estándar tecnológico del sector profesional de vigilancia aérea y emergencias.

El prototipo desarrollado en este proyecto réplica y adapta dichas funciones en una plataforma experimental de arquitectura abierta, integrando una cámara térmica, un sistema RGB, algoritmos de inteligencia artificial para detección de fuego y personas, navegación autónoma mediante Pixhawk y un sistema de comunicaciones de largo alcance basado en LoRa. Aunque no compite directamente con drones comerciales de alta gama, el prototipo busca demostrar la viabilidad técnica de un UAV autónomo capaz de cumplir misiones equivalentes en un contexto de bajo costo y orientado a validación académica.

### 5.1 Comparación con drones comerciales relevantes

A continuación, se presenta una tabla comparativa que resume las características principales de los drones comerciales más utilizados en tareas similares y su relación con el prototipo desarrollado:

Facultad de Ingeniería
Universidad Nacional de Lomas de Zamora

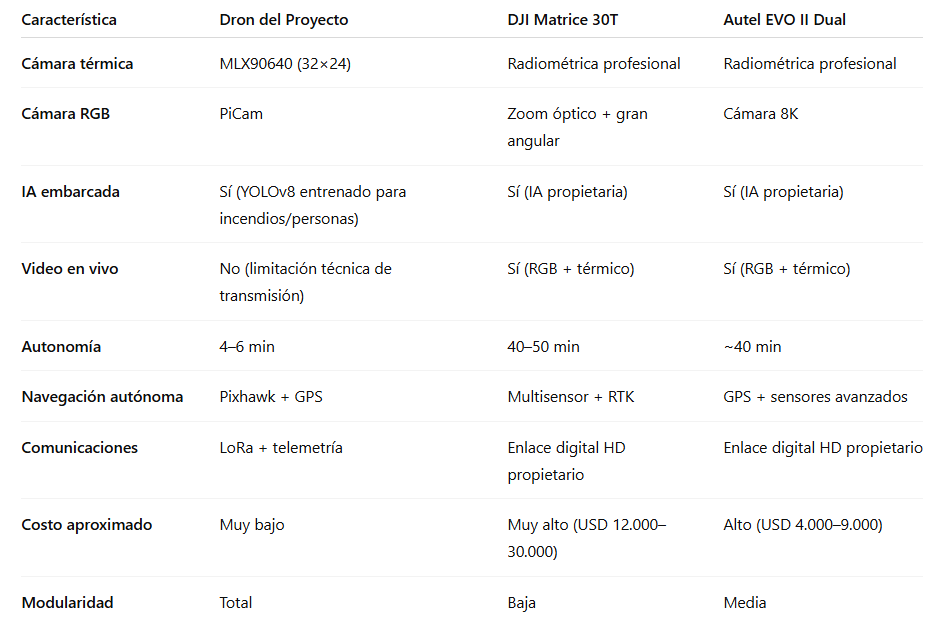
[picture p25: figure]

### 5.2 Diferencias funcionales relevantes

### 5.2.1 Ventaja del prototipo: IA entrenada específicamente para incendios y personas

A diferencia de los drones comerciales que incorporan modelos de IA genéricos y optimizados para una amplia variedad de escenarios, el prototipo desarrollado en este proyecto utiliza un modelo YOLOv8 entrenado específicamente para:

- Detección de focos de incendio
- Personas en entornos naturales

Este enfoque especializado permite adaptar el rendimiento del sistema a las necesidades concretas de la misión, aprovechando un pipeline completamente local (on-board processing) que no depende de servidores externos ni de enlaces de comunicación de alta velocidad.

### 5.2.2 Diferencia fundamental: falta de transmisión de video en vivo

Los drones comerciales de emergencia utilizan enlaces digitales de gran ancho de banda (como OcuSync o SkyLink) que permiten enviar video RGB y térmico en tiempo real hacia

Facultad de Ingeniería
Universidad Nacional de Lomas de Zamora
un | operador | remoto.
En contraste, el presente prototipo no transmite video en vivo, debido a:
| ● la baja capacidad de transmisión del módulo LoRa,
| ● las limitaciones energéticas del hardware embarcado,
- y la prioridad de diseño puesta en procesar imágenes a bordo y enviar solo alertas relevantes.

Sin embargo, esta restricción no afecta la misión propuesta, dado que el sistema está orientado a:

- capturas puntuales,
| ● procesamiento local mediante IA,
| ● y transmisión de eventos georreferenciados.

Este enfoque reduce consumo energético, complejidad del sistema y dependencia de infraestructura de comunicaciones externas.

Facultad de Ingeniería
Universidad Nacional de Lomas de Zamora

### 6. Presupuesto y Costos del Sistema Desarrollado

### 6.1 Componentes utilizados

El prototipo desarrollado integra una arquitectura abierta basada en sistemas embebidos, sensores térmicos y ópticos, actuadores brushless y una controladora de
vuelo | de | grado | hobby.
La siguiente tabla resume los componentes principales utilizados en la construcción del dron, incluyendo módulos electrónicos, sensores, actuadores y estructura portante.

Lista de componentes del sistema

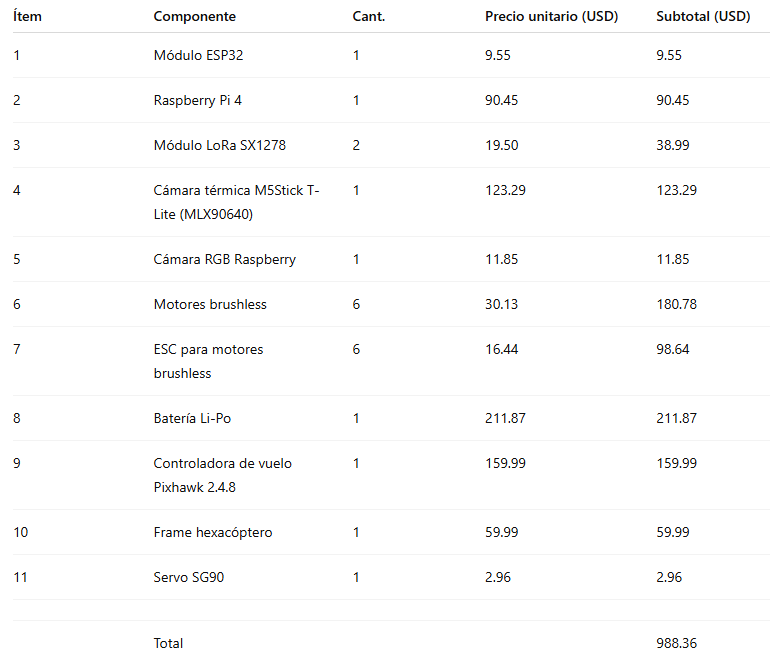
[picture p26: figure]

Este valor corresponde al costo directo del hardware requerido para el prototipo, excluyendo impresión 3D, consumibles, repuestos, herramientas y horas de trabajo técnico.

Facultad de Ingeniería
Universidad Nacional de Lomas de Zamora

### 6.2 Costos unitarios y costo total del prototipo

El costo total del sistema es de 988.86 USD, lo que lo posiciona como una plataforma de muy bajo costo comparada con los UAV comerciales destinados a tareas de emergencia y vigilancia ambiental.

Algunos puntos clave:

- La Raspberry Pi 4 representa una parte importante del costo, pero permite ejecutar IA embarcada sin necesidad de hardware propietario.
- La Pixhawk provee autonomía en vuelo similar a controladoras profesionales, manteniendo un costo accesible.
- La cámara térmica MLX90640, aunque de baja resolución, es significativamente más económica que las unidades radiométricas integradas en drones comerciales.
- El uso de LoRa reduce drásticamente costos de transmisión a cambio de sacrificar video en vivo.

El resultado es un sistema económicamente viable y orientado al prototipado académico, que integra tecnologías avanzadas a una fracción del costo de las soluciones comerciales.

### 6.3 Comparación económica con drones comerciales

Para contextualizar el costo del prototipo, se comparó el costo total del dron desarrollado con dos UAV comerciales ampliamente utilizados en operaciones de emergencia:

### 6.4 Conclusión comparativa y justificación económica del diseño

El análisis económico demuestra que el dron del proyecto representa una alternativa extremadamente accesible frente a los UAV comerciales utilizados en tareas de emergencia. Con un costo total aproximado de 990 USD, el prototipo equivale a:

- entre el 4% y el 10% del valor de un Autel EVO II Dual,

Facultad de Ingeniería
Universidad Nacional de Lomas de Zamora
- entre el 3% y el 9% del valor de un DJI Matrice 30T.

A pesar de esta diferencia económica significativa, el sistema desarrollado logra validar funciones esenciales presentes en estos equipos de alta gama, tales como:

- detección térmica,
- inteligencia artificial embarcada,
- navegación autónoma mediante GPS,
- transmisión remota de eventos y coordenadas georreferenciadas.

La viabilidad económica del proyecto se sustenta en decisiones de diseño orientadas a maximizar prestaciones con un presupuesto reducido. La selección de componentes accesibles —como ESP32, Raspberry Pi, Pixhawk y el sensor térmico MLX90640— permite construir un sistema completo sin depender de hardware propietario ni ecosistemas cerrados.

Asimismo, la modularidad de la arquitectura facilita el reemplazo, mejora y ampliación de sensores o procesadores, favoreciendo la experimentación y las iteraciones rápidas propias de entornos académicos. Este enfoque resulta especialmente adecuado para proyectos que requieren:

- múltiples ciclos de prueba y error,
- diagnóstico y modificación de subsistemas,
- integración incremental de nuevas capacidades.

En síntesis, aunque no pretende competir con las plataformas profesionales en términos de robustez o autonomía, el dron del proyecto ofrece una relación costo–prestación altamente favorable, demostrando que es posible integrar tecnologías avanzadas como visión térmica, IA embarcada y vuelo autónomo por una fracción del costo de los sistemas comerciales.

### 7. Arquitectura General del Sistema

La arquitectura del sistema desarrollado se basa en una estructura modular que integra sensores ópticos y térmicos, procesamiento inteligente mediante inteligencia artificial, comunicaciones de largo alcance y control de vuelo autónomo. Este enfoque permite distribuir las funciones entre distintos módulos especializados, facilitando el diseño, la depuración, la integración y la escalabilidad del prototipo.

El diagrama de bloques resume el funcionamiento general del sistema, en donde la Raspberry Pi, la ESP32 y la Pixhawk actúan como los tres nodos principales de

Facultad de Ingeniería
Universidad Nacional de Lomas de Zamora

procesamiento y control. En conjunto, estos módulos permiten ejecutar el flujo de misión: vuelo autónomo, captura de imágenes, análisis con IA, detección de eventos relevantes y transmisión de alertas hacia la estación base.

### 7.1 Arquitectura en Bloques del Sistema

El dron se organiza en torno a tres subsistemas principales:

1. Subsistema de detección (visión RGB + térmica)
- Captura de imágenes RGB mediante la PiCam.
- Lectura de la matriz térmica MLX90640.
- Procesamiento local por la Raspberry Pi para identificar fuego y personas.
2. Subsistema de control de misión
- La ESP32 recibe detecciones desde la Raspberry Pi.
- Envía comandos MAVLink hacia Pixhawk.
- Transmite alertas y coordenadas vía LoRa hacia la Ground Station.
3. Subsistema de vuelo autónomo
- La Pixhawk ejecuta ArduCopter 4.6.2.
- Controla motores y estabilización.
- Navega entre waypoints mediante GPS.


Facultad de Ingeniería
Universidad Nacional de Lomas de Zamora

Este diagrama permite visualizar cómo fluye la información a través del sistema: desde la captación de datos visuales, pasando por la inferencia de IA, hasta la transmisión de eventos y el control del vuelo autónomo.

### 7.2.1 Controladora de Vuelo Pixhawk 2.4.8

La Pixhawk constituye el núcleo de control aeronáutico del dron. Ejecuta el firmware ArduCopter 4.6.2, el cual proporciona:

- estabilización y control en tiempo real,
- control de velocidad de motores mediante los ESC,
- gestión de sensores inerciales y de navegación,
- modos de vuelo autónomos (GUIDED, AUTO, LOITER, RTL),
- Recepción de comandos vía MAVLink desde la ESP32.

La Pixhawk se encarga de la ejecución segura de la misión, asegurando que el dron despegue, navegue entre waypoints y aterrice de manera estable.

### 7.2.2 Módulo ESP32

La ESP32 funciona como unidad de control intermedia entre la Raspberry Pi y la Pixhawk.
Sus funciones principales son:
- interpretar las detecciones enviadas por la Raspberry Pi mediante UART,
- tomar decisiones de misión (detener vuelo, reenviar eventos, continuar ruta),
- transmitir eventos y coordenadas mediante el módulo LoRa SX1278,
- enviar comandos MAVLink a la Pixhawk (takeoff, set waypoint, RTL, land).

Este módulo representa el “cerebro lógico” del dron, encargado de supervisar y coordinar el comportamiento global durante la misión.

### 7.2.3 Raspberry Pi 4

La Raspberry Pi es la encargada de ejecutar el procesamiento inteligente del sistema. Sus funciones incluyen:

- captura de imágenes RGB y térmicas,
- preprocesamiento de datos (reescalado, normalización, matrices térmicas),

Facultad de Ingeniería
Universidad Nacional de Lomas de Zamora
- ejecución del modelo YOLOv8 en formato ONNX,
- detección de fuego y personas,
- Envío de alertas a la ESP32.

Su capacidad de cómputo permite implementar un esquema de edge computing, procesando la información en tiempo real sin necesidad de transmisión de video continuo.

### 7.2.4 Módulo LoRa SX1278

El módulo LoRa permite la comunicación de largo alcance entre el dron y la Ground Station, garantizando transmisión aún en zonas rurales o de vegetación densa. Características relevantes:

- bajo consumo energético,
- largo alcance,
- no apto para transmisión de video, solo datos discretos,
- ideal para enviar alertas con coordenadas.

LoRa actúa como el enlace principal para la notificación de detecciones relevantes.

### 7.2.5 Cámaras RGB e Infrarroja

PiCam (RGB)
- Captura imágenes en puntos específicos de la misión (waypoints).
- Permite identificar personas, fuego visible y humo.

MLX90640 (IR)
- Matriz térmica de 32×24 píxeles.
- Ideal para detectar variaciones de temperatura asociadas a incendios o presencia humana.
- Permite confirmación térmica de detecciones ambiguas en RGB.

### 7.3 Flujo de Misión del Sistema Completo

El proceso operativo del sistema comienza en la Ground Station y continúa a bordo del dron a través de los módulos ESP32, Raspberry Pi y Pixhawk. El flujo completo se describe a continuación.

Facultad de Ingeniería
Universidad Nacional de Lomas de Zamora

### 1. Definición del polígono o área de interés

En la Ground Station, el operador selecciona un polígono geográfico que delimita la zona a inspeccionar, detallando, además, altura de vuelo, espaciado entre pasadas, espaciado entre detecciones y el comportamiento frente a la detección de un evento (continuar la misión navegando waypoints o volver a home).
El sistema genera automáticamente la secuencia de waypoints necesarios para cubrir el área, mostrando a medida que se realizan ajustes cómo se modifica la ruta y dichos waypoints.

### 2. Armado del dron y checklist de pre-vuelo

Antes de iniciar la misión, el equipo realiza las verificaciones correspondientes:

- conexión de baterías,
- verificación de sensores,
- bloqueo/armado de motores,
- comunicación Pixhawk–ESP32–Raspberry Pi–LoRa.

Cuando el sistema valida todos los parámetros, el dron queda listo para iniciar la misión.

### 3. Envío del plan de vuelo a la Pixhawk

La ESP32 recibe desde la Ground Station la lista de waypoints generada por trozos compatible con el tamaño máximo seguro de envío de datos por LoRa, concatena esos mensajes en orden y los transmite de a uno a la Pixhawk mediante MAVLink.
El dron queda configurado en modo GUIDED.

### 4. Despegue automático

La Pixhawk recibe desde la ESP32 el comando de despegue. El dron asciende hasta la altura programada.

### 5. Navegación al primer waypoint

La Pixhawk guía el dron empleando GPS y control de altitud.

### 6. Detención y estabilización en waypoint

Al alcanzar cada punto, la ESP32 ordena al dron detenerse para realizar captura y análisis.

### 7. Captura de datos RGB + térmico

La Raspberry Pi adquiere imágenes RGB y una matriz térmica completa del MLX90640.

Facultad de Ingeniería
Universidad Nacional de Lomas de Zamora

### 8. Procesamiento local con IA

La Raspberry Pi ejecuta el modelo YOLOv8 (formato ONNX) para identificar:

- fuego
- personas

### 9. Envío de detecciones a la ESP32

Si se detecta un evento, la Raspberry Pi informa a la ESP32 mediante UART con la etiqueta de la detección y nivel de confianza. Si ocurre una detección del tipo persona, soltara el paquete que lleva el gripper.

### 10. Transmisión de alerta a la Ground Station

La ESP32 envía vía LoRa:

- tipo de detección,
- coordenadas del dron,
- timestamp y meta-información.

Esto permite al operador visualizar el evento en tiempo real sobre el mapa y tomar acción respecto del problema detectado.

### 11. Continuación de la misión

Una vez finalizado el análisis, la ESP32 ordena reanudar el vuelo hacia el siguiente waypoint o bien regresar a la base, según como haya seteado el programa el operador.

### 12. Finalización de la misión y retorno automático

Al completar la ruta, la ESP32 envía la coordenada de home a la Pixhawk como si fuese un waypoint más, y luego ejecuta el aterrizaje.

Facultad de Ingeniería
Universidad Nacional de Lomas de Zamora

### 8. Desarrollo de los Subsistemas

El sistema desarrollado se compone de múltiples subsistemas que actúan de manera coordinada para ejecutar la misión autónoma. Cada uno cumple una función específica dentro del flujo percepción–procesamiento–decisión–acción. A continuación, se describen los subsistemas principales, sus características técnicas y su integración dentro de la arquitectura general.

### 8.1 Sistema de detección autónoma de personas y/o fuego


Para la implementación del sistema de visión y detección, se diseñó una arquitectura de software modular distribuida en tres bloques lógicos principales que operan de manera cooperativa. Esta estructura permite separar las tareas de adquisición de datos en tiempo real del procesamiento computacional intensivo, asegurando que el procesamiento pesado de las imágenes no detenga la ejecución del resto del sistema. Esto permite seguir recibiendo datos de los sensores y mantener la conexión fluida con el dron sin tener que esperar a que finalice cada inferencia de la inteligencia artificial.

Adicionalmente, esta división operativa ofrece una ventaja significativa en la gestión del software: el aislamiento de entornos. Cada código se ejecuta en su propio entorno virtual independiente, lo que evita conflictos entre versiones incompatibles de las mismas librerías. De esta manera, cada subsistema cuenta con las dependencias exactas que necesita, sin que las actualizaciones requeridas por el modelo de IA comprometan la estabilidad de los controladores de los sensores.

El flujo de información comienza en el nivel de hardware con el firmware del M5StickC, el cual actúa como un dispositivo de adquisición dedicado para el sensor térmico. En el siguiente nivel, ejecutándose sobre la Raspberry Pi, el Código 1 (Módulo de captura y análisis térmico) funciona como el orquestador principal: solicita los datos térmicos,

Facultad de Ingeniería
Universidad Nacional de Lomas de Zamora

captura las imágenes visuales RGB y realiza un primer filtrado de alertas basado en temperatura.

Finalmente, la integración entre la visión clásica y la inteligencia artificial se logra mediante un esquema asíncrono basado en el sistema de archivos. Cuando el Código 1 deposita una imagen en la carpeta compartida, se dispara automáticamente al Código 2 (Análisis con IA). Este último módulo procesa la imagen con el modelo YOLOv8 y, en caso de confirmar una detección positiva, emite las alertas correspondientes al sistema de control, cerrando así el ciclo de vigilancia autónoma detallado en el siguiente esquema global.


Facultad de Ingeniería
Universidad Nacional de Lomas de Zamora
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

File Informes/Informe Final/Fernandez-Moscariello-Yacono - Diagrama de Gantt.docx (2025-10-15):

PROYECTO FINAL MECATRONICA

CRONOGRAMA DEL PROYECTO

DIAGRAMA DE GANTT


Profesores:

Ing. Blanca, Ezequiel

Ing. Lukaszewicz, Cristian Leandro

Ing. Szombach, Juan Ignacio

Alumnos:

Fernandez Malenotti, Ignacio

Moscariello, Christian

Yacono, Emiliano

Universidad Nacional de Lomas de Zamora Facultad de Ingeniería

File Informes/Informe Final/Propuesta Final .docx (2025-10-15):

PROYECTO FINAL MECATRONICA


Profesores:

Ing. Blanca, Ezequiel

Ing. Lukaszewicz, Cristian Leandro

Ing. Szombach, Juan Ignacio

Alumnos:

Fernandez Malenotti, Ignacio

Moscariello, Christian

Yacono, Emiliano

# Propuesta Final

## Título del Proyecto

Dron Autónomo para Detección de Incendios y Rescate de Personas

## Motivación y Antecedentes

Durante el verano, zonas de parques nacionales y áreas de montaña enfrentan dos problemáticas críticas:

1. La aparición de focos de incendio, que pueden propagarse rápidamente debido a la vegetación seca.
2. El extravío de personas en zonas de difícil acceso, como bosques y áreas montañosas.

Actualmente, la cobertura de grandes extensiones con personal reducido dificulta las tareas de vigilancia, control y rescate. Esto retrasa la respuesta inicial ante un incendio o la localización de personas, aumentando riesgos y daños. Además, el coste de patrullaje de un helicóptero es elevado y su espacio aéreo de observación acotado.

## Descripción de la Propuesta

Se propone el desarrollo de un prototipo de dron autónomo a escala, capaz de:

1. Detectar visual y térmicamente focos de incendio en su etapa inicial.
2. Localizar personas extraviadas mediante análisis de imagen e infrarrojo.
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

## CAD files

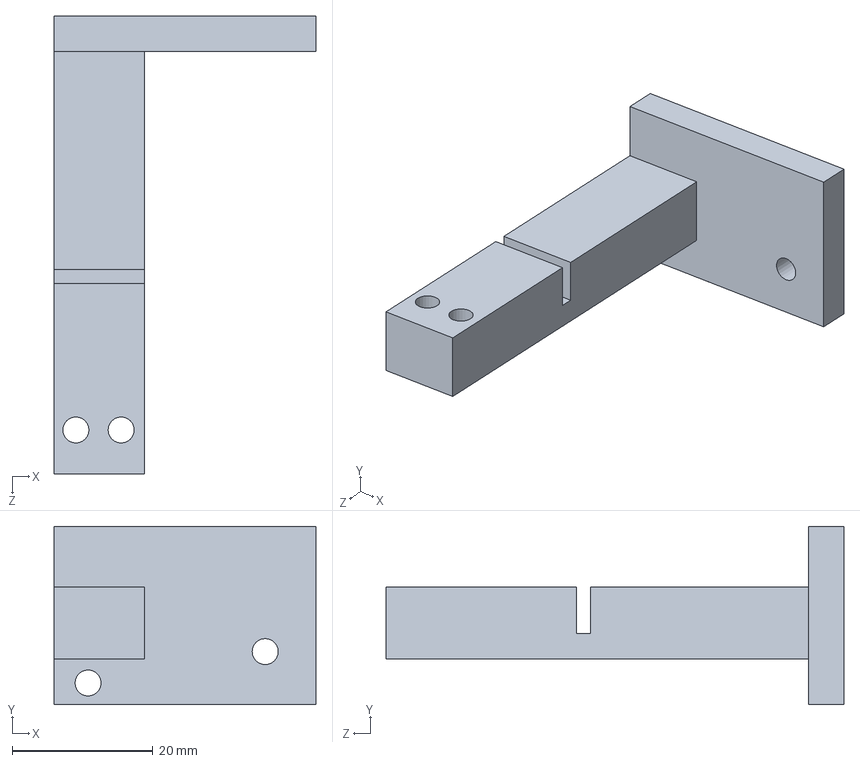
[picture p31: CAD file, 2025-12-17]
Modelado 3D/armado definitivo/cuerpo final/soporteplacas1^Ensamblaje1.sldprt
37.2 x 25.3 x 65.0 mm

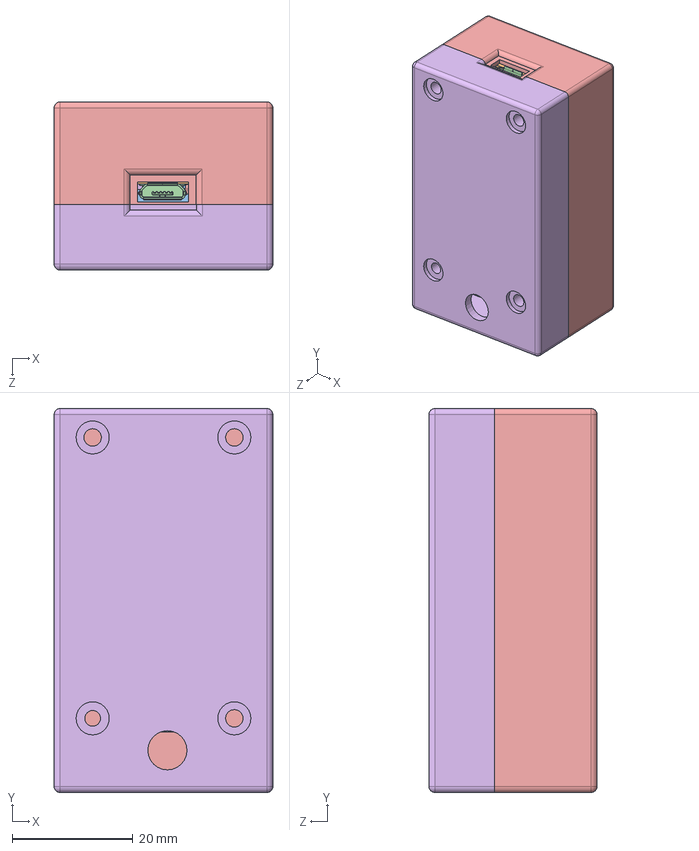
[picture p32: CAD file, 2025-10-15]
Modelado 3D/armado definitivo/esp32-lora-base/Ensamblaje1.SLDASM
36.3 x 63.7 x 27.9 mm
Body001.step x 30
________________ __________.step
ESP32-WROOM-32.step
USB_Micro-B_Molex_47346-0001.step
AMS-1117.step
cp2102.step
SOT_23-1.step
SOT_23-2.step
SW_SPST_B3U-1000P-1.step
SW_SPST_B3U-1000P-2.step
CP_EIA_3216_10_Kemet_I.step
lora-ra-02-ai-thinker.step
Pieza13
Pieza16

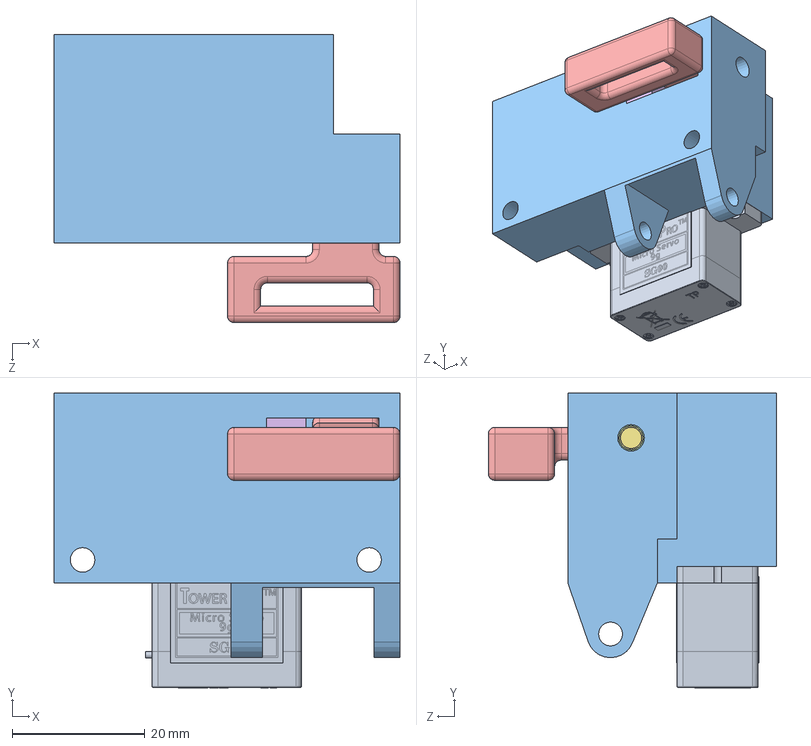
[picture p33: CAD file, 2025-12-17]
Modelado 3D/armado definitivo/griper/Ensamblaje1.SLDASM
52.2 x 44.5 x 43.5 mm
SG90 - Micro Servo 9g - Tower Pro.1
SG90 - Micro Servo 9g - Tower Pro.2
Pieza1^Ensamblaje1
Pieza2^Ensamblaje1
gancho^Ensamblaje1
tope^Ensamblaje1
Pieza3^Ensamblaje1

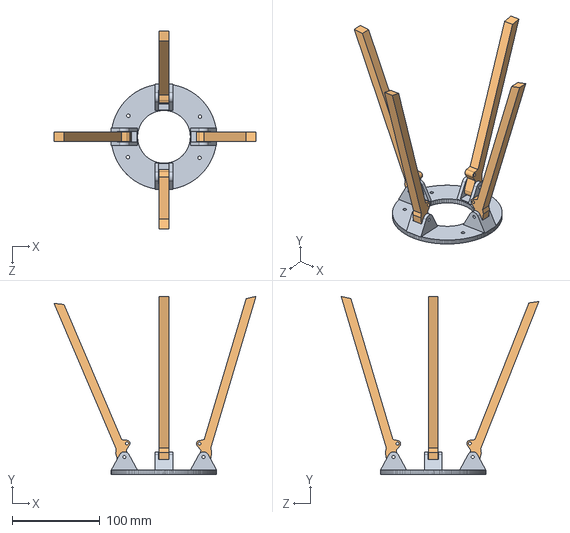
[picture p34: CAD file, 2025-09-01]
Modelado 3D/versiones previas/base aterrizaje/Ensamblaje tren aterrizaje.SLDASM
229.6 x 202.6 x 224.8 mm
base
pata x 4

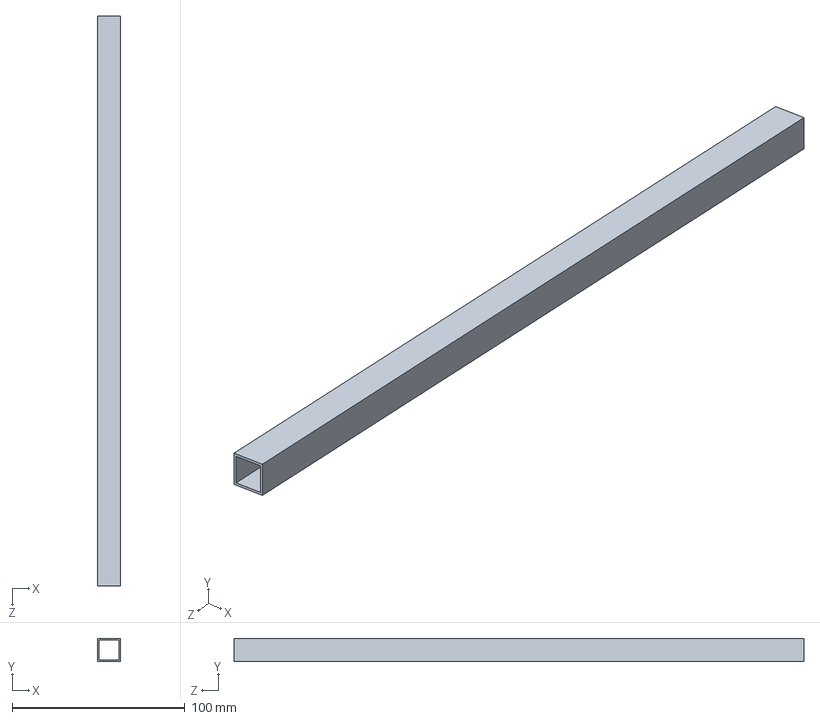
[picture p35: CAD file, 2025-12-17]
Modelado 3D/armado definitivo/cuerpo final/barra motor^Ensamblaje1.sldprt
13.5 x 13.5 x 330.0 mm

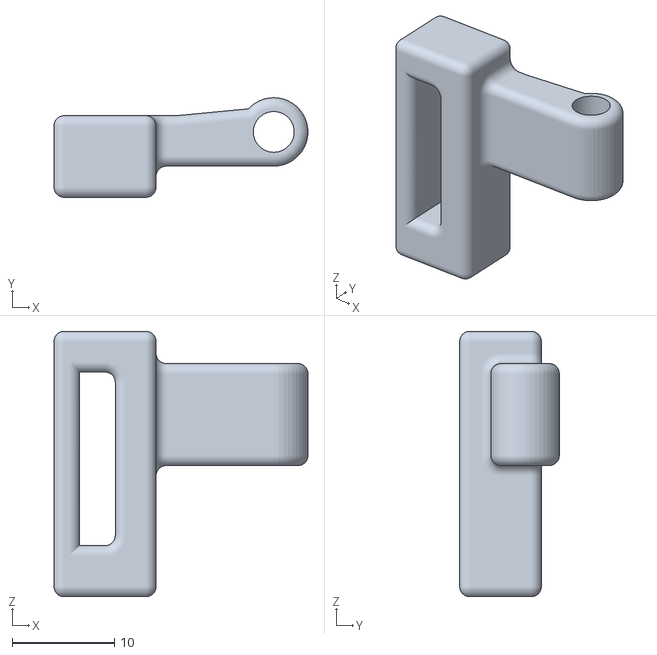
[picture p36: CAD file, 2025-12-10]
Modelado 3D/armado definitivo/griper/gancho^Ensamblaje1.STL
24.9 x 9.76 x 26.0

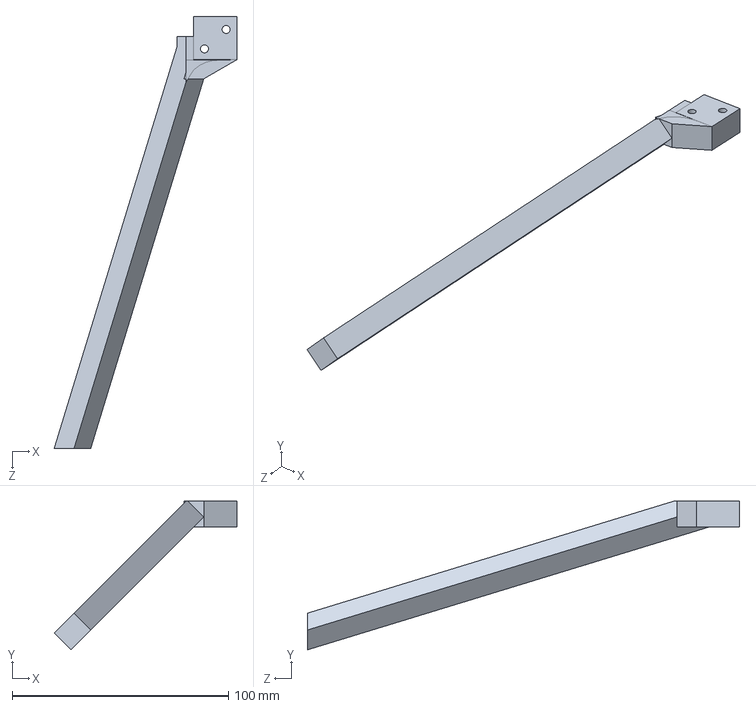
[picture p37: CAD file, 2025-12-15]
Modelado 3D/armado definitivo/cuerpo final/pata45^Ensamblaje1.sldprt
84.6 x 68.8 x 200.0 mm

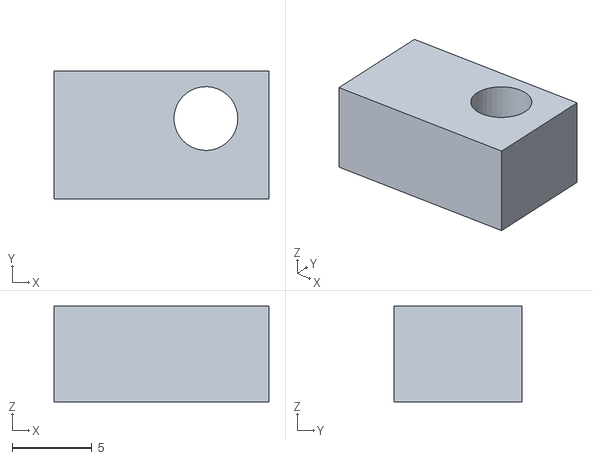
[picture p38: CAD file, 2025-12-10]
Modelado 3D/armado definitivo/griper/tope^Ensamblaje1.STL
13.5 x 8.00 x 6.00

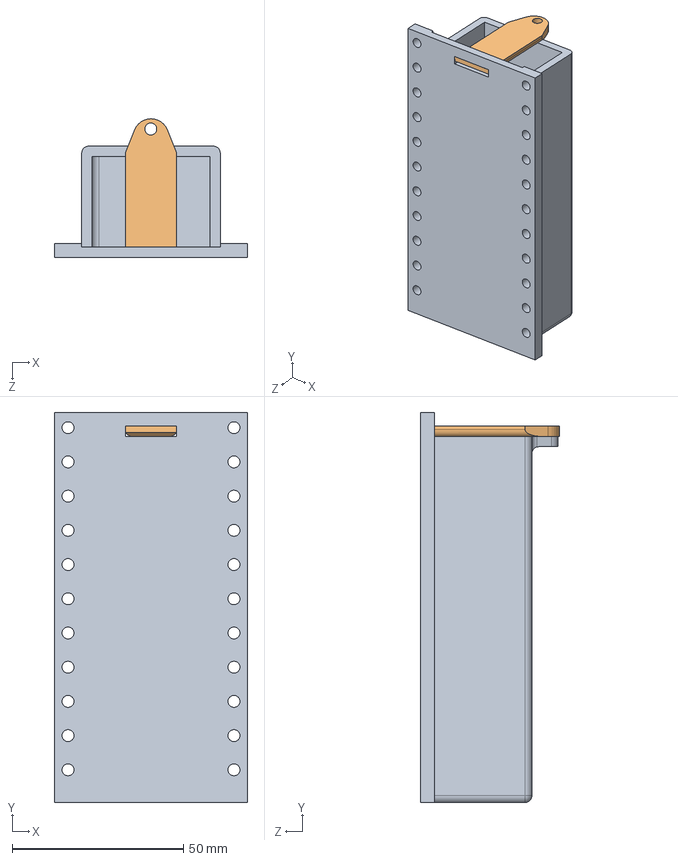
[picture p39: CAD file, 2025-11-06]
Modelado 3D/versiones previas/batria/Ensamblajebat.SLDASM
56.5 x 114.0 x 40.5 mm
soporte bateria
Pieza3

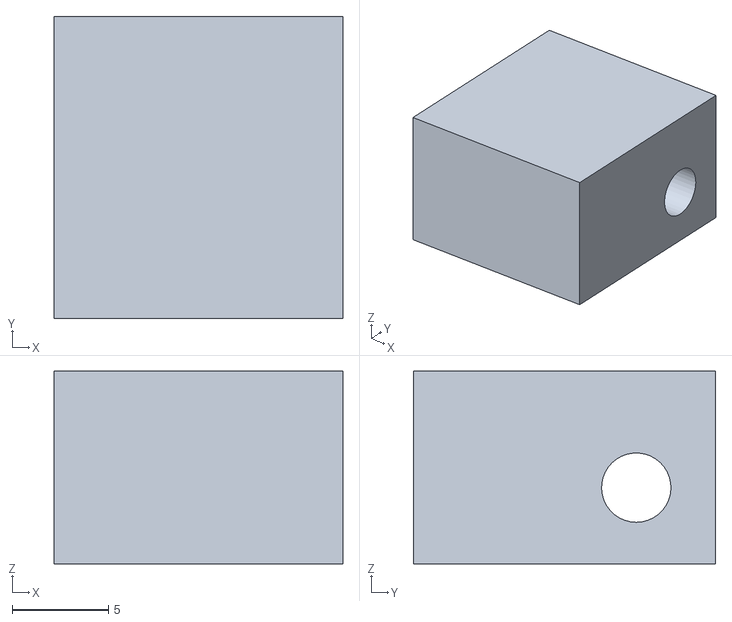
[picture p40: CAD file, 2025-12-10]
Modelado 3D/armado definitivo/griper/Pieza2^Ensamblaje1.STL
15.0 x 15.7 x 10.00

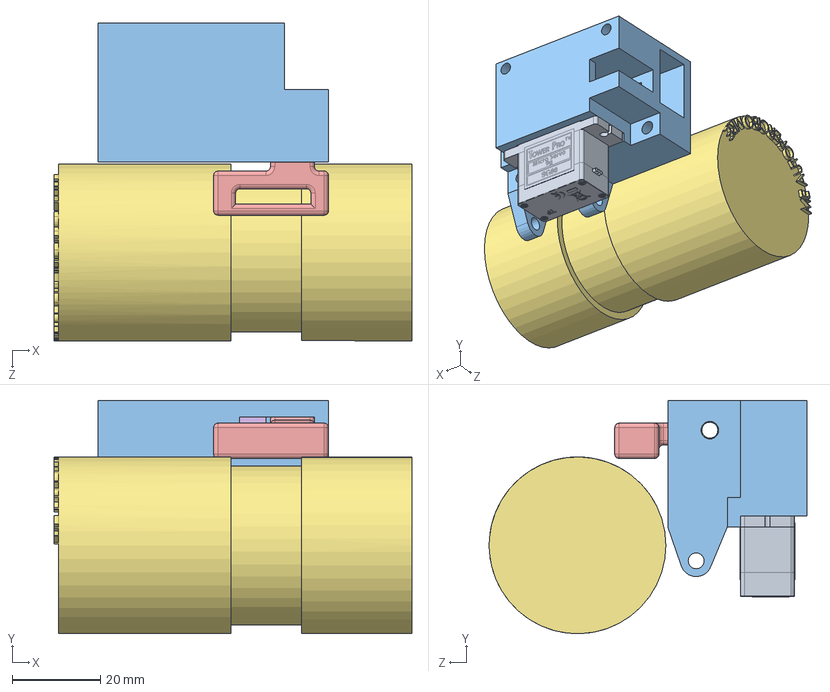
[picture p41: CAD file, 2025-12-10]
Modelado 3D/armado definitivo/griper/ensamble gripper.SLDASM
81.0 x 52.8 x 71.9 mm
SG90 - Micro Servo 9g - Tower Pro.1
SG90 - Micro Servo 9g - Tower Pro.2
Pieza1^ensamble gripper
Pieza2^ensamble gripper
gancho^ensamble gripper
tope^ensamble gripper
Coso para transportar

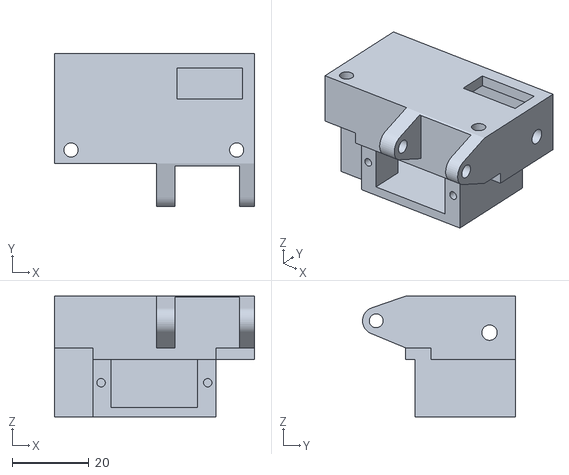
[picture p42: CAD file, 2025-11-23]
Modelado 3D/armado definitivo/griper/Pieza1^Ensamblaje1.STL
52.2 x 39.9 x 31.5

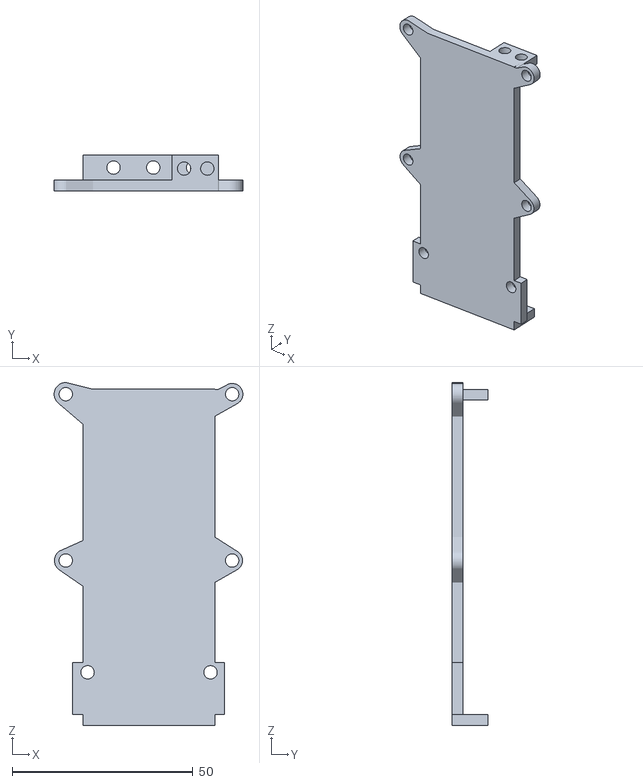
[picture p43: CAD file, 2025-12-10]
Modelado 3D/armado definitivo/cuerpo final/basecamaras-gripper^Ensamblaje1.STL
52.2 x 10.00 x 94.9

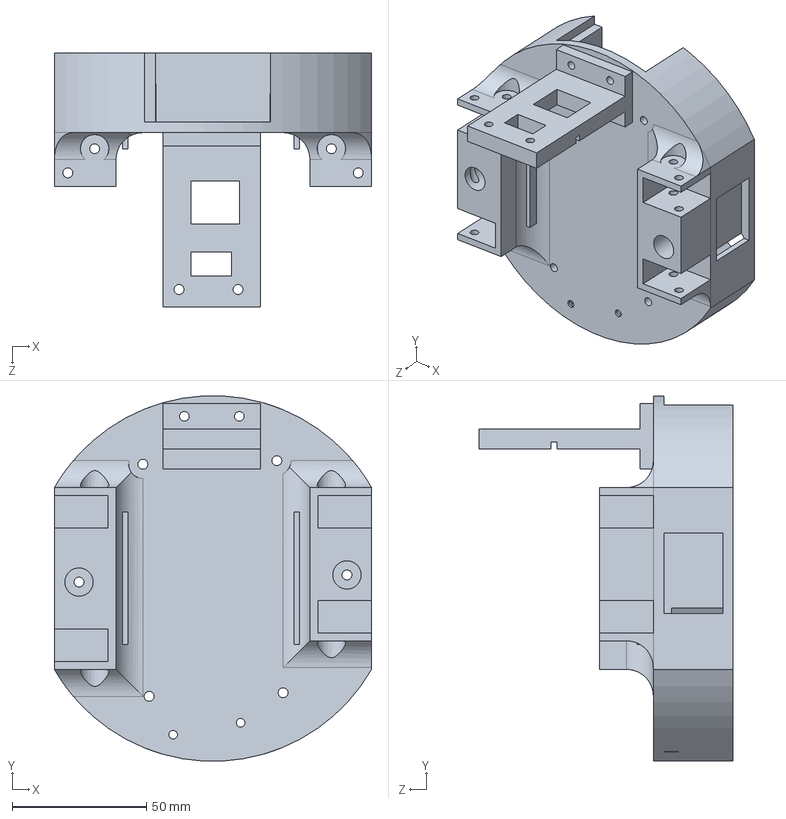
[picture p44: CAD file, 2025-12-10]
Modelado 3D/armado definitivo/cuerpo final/base^Ensamblaje1.sldprt
118.3 x 136.2 x 94.7 mm

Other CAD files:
Modelado 3D/armado definitivo/Soporte camaras/Soporte camaras.SLDASM
Modelado 3D/armado definitivo/cuerpo final/Simetríapata45^Ensamblaje1.sldprt
Camara termografica/Area de cobertura MLX90640.dwg
Modelado 3D/armado definitivo/antenas/antenalora.SLDPRT
Modelado 3D/armado definitivo/Soporte camaras/Carcaza.SLDPRT
Modelado 3D/armado definitivo/Soporte camaras/Carcaza.STEP
Modelado 3D/armado definitivo/Soporte camaras/Carcaza.STL
Modelado 3D/armado definitivo/Soporte camaras/M5 Stick.SLDPRT
Modelado 3D/armado definitivo/Soporte camaras/M5 Stick.STEP
Modelado 3D/armado definitivo/Soporte camaras/OV5647.SLDPRT
Modelado 3D/armado definitivo/Soporte camaras/OV5647.STEP
Modelado 3D/armado definitivo/Soporte camaras/Tapa.SLDPRT
Modelado 3D/armado definitivo/Soporte camaras/Tapa.STEP
Modelado 3D/armado definitivo/Soporte camaras/Tapa.STL
Modelado 3D/armado definitivo/antenas/antenalora.STL
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

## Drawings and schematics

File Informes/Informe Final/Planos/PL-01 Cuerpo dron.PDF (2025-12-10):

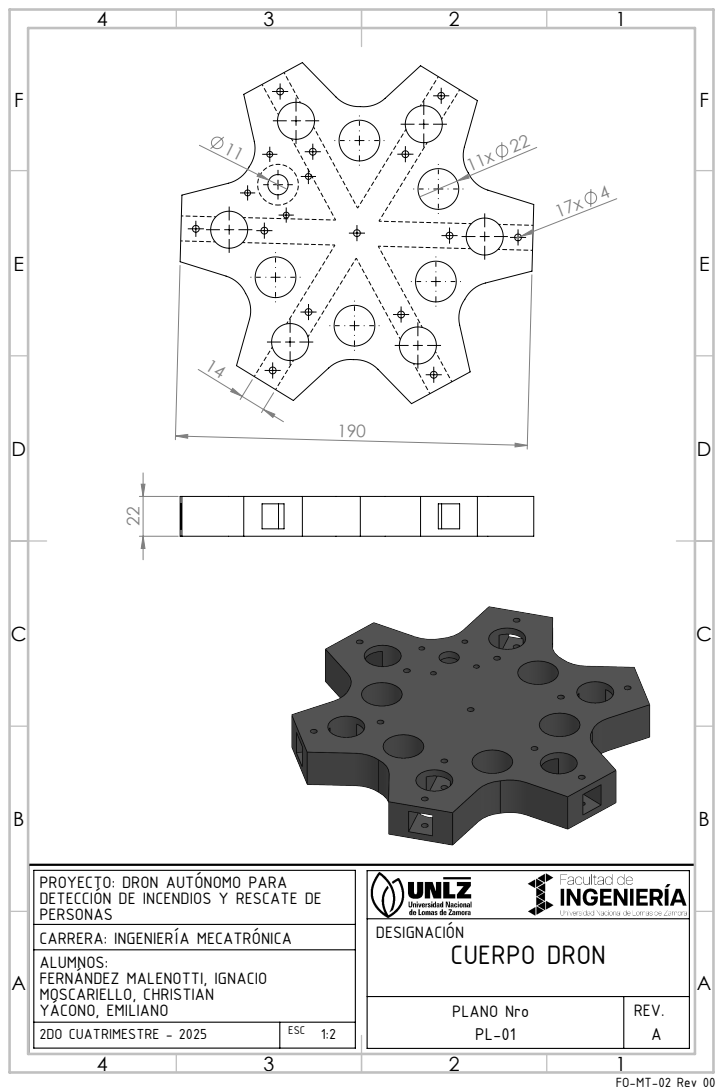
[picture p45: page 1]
CUERPO DRON

PROYECTO: DRON AUTÓNOMO PARA DETECCIÓN DE INCENDIOS Y RESCATE DE
PERSONAS
CARRERA: INGENIERÍA MECATRÓNICA
ALUMNOS: FERNÁNDEZ MALENOTTI, IGNACIO
MOSCARIELLO, CHRISTIAN YÁCONO, EMILIANO

PLANO Nro PL-01 | REV. A

2DO CUATRIMESTRE - 2025 | ESC 1:2

FO-MT-02 Rev 00

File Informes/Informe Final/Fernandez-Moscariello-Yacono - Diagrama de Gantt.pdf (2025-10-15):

Universidad Nacional de Lomas de Zamora Facultad de Ingeniería

1

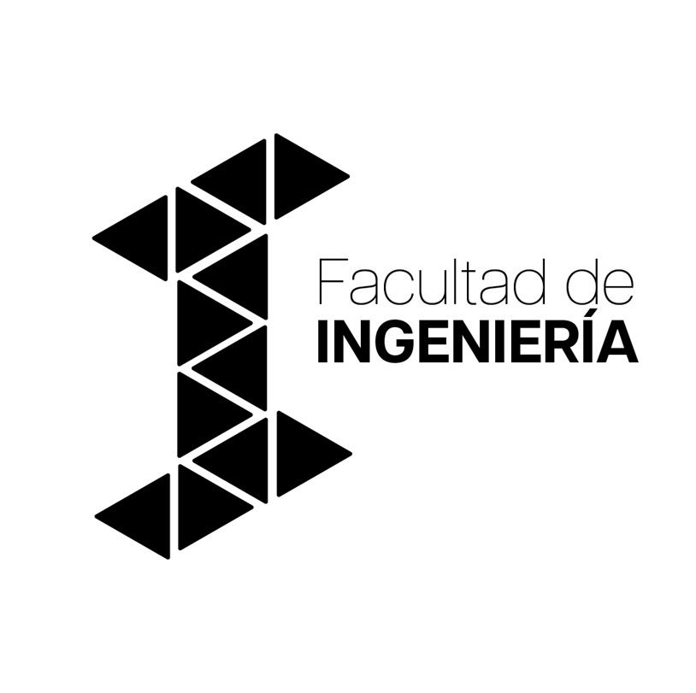
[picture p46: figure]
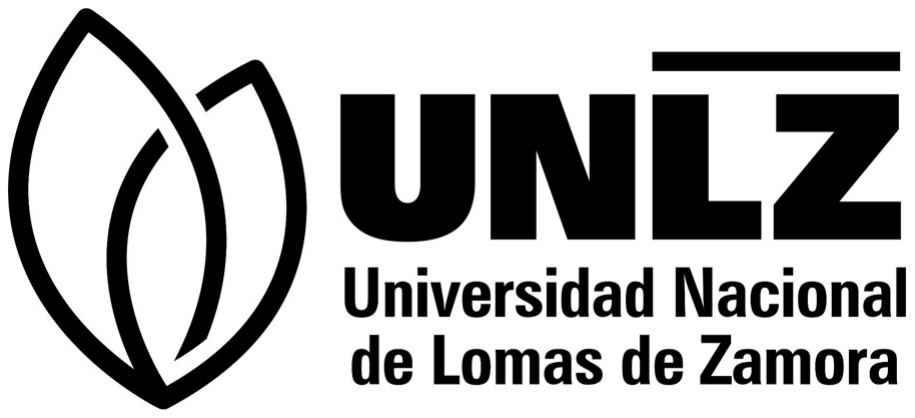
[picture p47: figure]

PROYECTO FINAL MECATRONICA CRONOGRAMA DEL PROYECTO
DIAGRAMA DE GANTT

Profesores:

Ing. Blanca, Ezequiel
Ing. Lukaszewicz, Cristian Leandro Ing. Szombach, Juan Ignacio

Alumnos:

Fernandez Malenotti, Ignacio Moscariello, Christian
Yacono, Emiliano

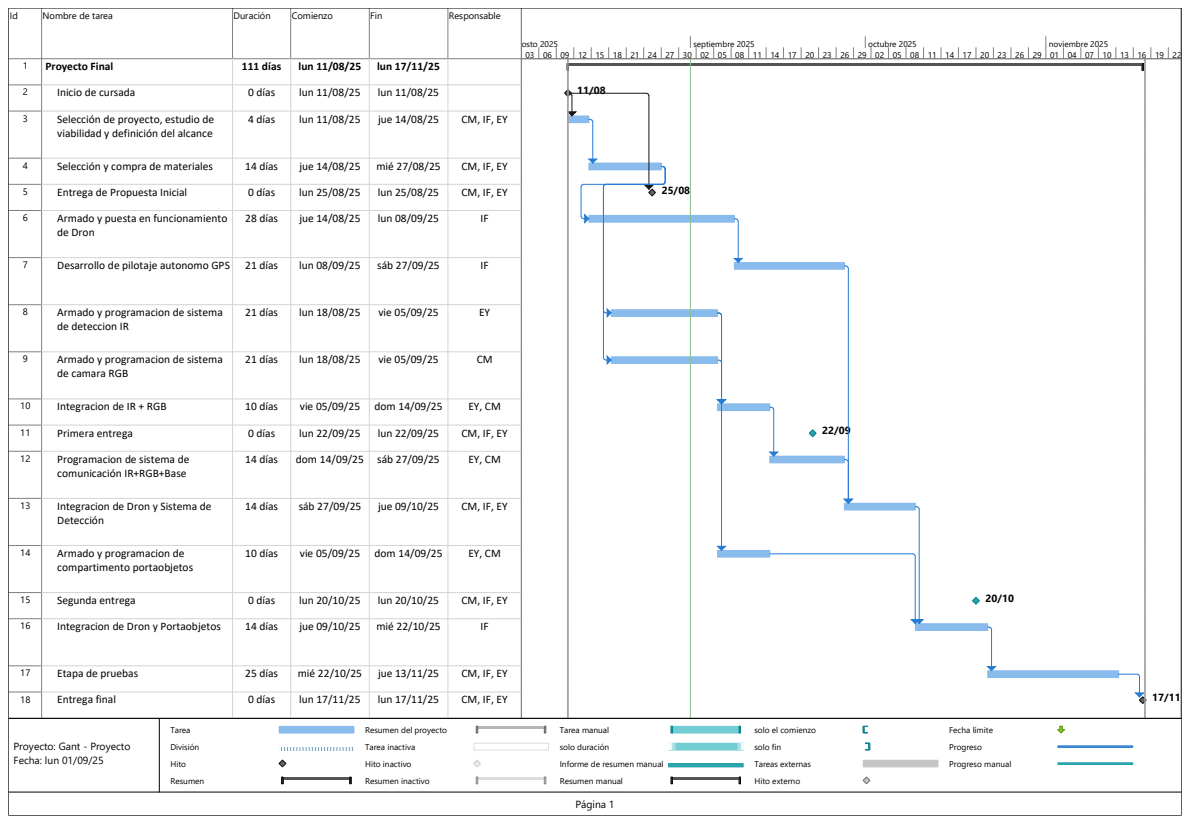
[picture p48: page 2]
agosto 2025; septiembre 2025; octubre 2025; noviembre 2025; Tarea; División; Resumen; Resumen inactivo; Tarea manual; solo duración; Resumen manual; Hito externo; Fecha límite; Progreso; Página 1

Id | Nombre de tarea | Duración | Comienzo | Fin | Responsable

1 | Proyecto Final | 111 días | lun 11/08/25 | lun 17/11/25
2 | Inicio de cursada | 0 días | lun 11/08/25 | lun 11/08/25
3 Selección de proyecto, estudio de | viabilidad y definición del alcance | 4 días | lun 11/08/25 | jue 14/08/25 | CM, IF, EY

4 | Selección y compra de materiales | 14 días | jue 14/08/25 | mié 27/08/25 | CM, IF, EY
5 | Entrega de Propuesta Inicial | 0 días | lun 25/08/25 | lun 25/08/25 | CM, IF, EY
6 Armado y puesta en funcionamiento | de Dron | 28 días | jue 14/08/25 | lun 08/09/25 | IF

7 | Desarrollo de pilotaje autonomo GPS | 21 días | lun 08/09/25 | sáb 27/09/25 | IF

8 Armado y programacion de sistema | de deteccion IR | 21 días | lun 18/08/25 | vie 05/09/25 | EY

9 Armado y programacion de sistema | de camara RGB | 21 días | lun 18/08/25 | vie 05/09/25 | CM

10 | Integracion de IR + RGB | 10 días | vie 05/09/25 | dom 14/09/25 | EY, CM
11 | Primera entrega | 0 días | lun 22/09/25 | lun 22/09/25 | CM, IF, EY
12 Programacion de sistema de | comunicación IR+RGB+Base | 14 días | dom 14/09/25 | sáb 27/09/25 | EY, CM

13 Integracion de Dron y Sistema de | Detección | 14 días | sáb 27/09/25 | jue 09/10/25 | CM, IF, EY

14 Armado y programacion de | compartimento portaobjetos | 10 días | vie 05/09/25 | dom 14/09/25 | EY, CM

15 | Segunda entrega | 0 días | lun 20/10/25 | lun 20/10/25 | CM, IF, EY
16 | Integracion de Dron y Portaobjetos | 14 días | jue 09/10/25 | mié 22/10/25 | IF

17 | Etapa de pruebas | 25 días | mié 22/10/25 | jue 13/11/25 | CM, IF, EY
18 | Entrega final | 0 días | lun 17/11/25 | lun 17/11/25 | CM, IF, EY

Resumen del proyecto
Tarea inactiva

solo el comienzo
solo fin

Proyecto: Gant - Proyecto Fecha: lun 01/09/25 | Hito Hito inactivo Informe de resumen manual Tareas externas Progreso manual

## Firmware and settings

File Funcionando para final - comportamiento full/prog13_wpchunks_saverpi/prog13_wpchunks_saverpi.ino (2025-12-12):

#include <Arduino.h>
#include <SPI.h>
#include <LoRa.h>
#include <ArduinoJson.h>
#include <math.h>
#include <vector>
#include <HardwareSerial.h>
#include <MAVLink.h>   
#include <ESP32Servo.h>

using std::vector;

#ifndef M_PI
#define M_PI 3.14159265358979323846
#endif

// ============================================================================
// 🛰️ CONFIGURACIÓN DE HARDWARE
// ============================================================================

// --- LoRa ---
#define LORA_CS  5
#define LORA_RST 14
#define LORA_IRQ 34
#define LORA_BAND 433E6

static const char* GS_HDR  = "GS#";
static const char* UAV_HDR = "UAV#";
static const char* SFX     = "#END";

String loraRxBuf;

// --- UART Raspberry ---
#define RPI_RX  32
#define RPI_TX  33
HardwareSerial SerialRPI(1);
#define RPI_BUFFER_SIZE 256
#define RPI_TIMEOUT_MS  50
char  rpiBuffer[RPI_BUFFER_SIZE];
size_t rpiIndex = 0;
bool  receivingJson = false;

// --- Pixhawk MAVLink ---
#define MAV_RX 16   // ESP32 RX ← Pixhawk TX (TELEM2)
#define MAV_TX 17   // ESP32 TX → Pixhawk RX (TELEM2)
HardwareSerial SerialMAV(2);
unsigned long lastGotoMs = 0;
static unsigned long lastHbMs = 0;

//failsafe bateria
bool battery_failsafe_active = false;
const float LOW_VOLTAGE_THRESHOLD = 11.1; // ajustar si querés

//arm
bool awaitingFastArmConfirm = false;
unsigned long armingConfirmationDeadline = 0;

// ============================================================================
// ⚙️ SERVO DE ACCIÓN (detección PERSON)
// ============================================================================
Servo actionServo;

const int SERVO_PIN = 25;      // GPIO donde conectás el servo
const int SERVO_CLOSED = 105;    // grados (cerrado)
const int SERVO_OPEN   = 35;   // grados (abierto)

bool servoActive = false;
unsigned long servoOpenStartMs = 0;
const unsigned long SERVO_OPEN_TIME = 30000;  // 30 segundos

// ============================================================================
// 📌 ESTRUCTURAS Y ESTADO GLOBAL
// ============================================================================

struct Coordinate {
  double lat;
  double lon;
};

struct Mission {
  bool loaded = false;
  vector<Coordinate> polygon;
  Coordinate home;
  double altitude = 0.0;
  double spacing  = 0.0;
  double detect_spacing = 5.0;   // spacing interno entre detecciones
  String event_action;     // "RETURN", "CONTINUE", etc.
} mission;

//---variables parser mavlink
// HEARTBEAT
uint8_t mav_type = 0;
uint8_t mav_autopilot = 0;
uint8_t mav_base_mode = 0;
uint32_t mav_custom_mode = 0;
uint8_t mav_system_status = 0;
bool mav_armed = false;

// GLOBAL POSITION
double mav_lat = 0, mav_lon = 0;
double mav_alt_rel = 0;
double mav_alt_abs = 0;
double mav_ground_speed = 0;
double mav_heading_deg = 0;
double mav_climb_rate = 0;
bool mav_has_fix = false;
unsigned long mav_last_update_ms = 0;

// BATTERY / SYS_STATUS
float mav_batt_voltage = 0.0f;
float mav_batt_current = 0.0f;
int   mav_batt_remaining = -1;

// Máximos ajustables RECEPCION WP CHUNKS
static const int MAX_MISSION_CHUNKS = 64;

String missionChunks[MAX_MISSION_CHUNKS];
bool   missionChunkReceived[MAX_MISSION_CHUNKS];
int    missionExpectedChunks = 0;
int    missionTotalWPs = 0;

bool   missionHasHeader = false;
bool   missionReady = false;

unsigned long missionLastChunkTime = 0;
const unsigned long MISSION_TIMEOUT = 3000;   // 3s → timeout para chunk faltante

// Traduce el custom_mode de ArduCopter a texto legible
String decodeFlightMode(uint32_t m) {
    switch (m) {
        case 0:  return "STABILIZE";
        case 3:  return "AUTO";
        case 4:  return "GUIDED";
        case 5:  return "LOITER";
        case 6:  return "RTL";
        default: return "UNKNOWN";
    }
}

// =======================
// 🛰️ Filtro GPS (tu versión)
// =======================
double lat_window[4] = {0};
double lon_window[4] = {0};
double alt_window[4] = {0};
int    win_idx = 0;

double lat_f = 0.0, lon_f = 0.0, alt_f = 0.0;
bool   have_filter = false;
int    gpsWarmup   = 0;
const double MAX_JUMP_DEG = 0.00030; // ~33 m

// =======================
// ⛓️ ACK LoRa
// =======================
struct PendingMsg {
  String payload;
  unsigned long lastSend;
  int  retries;
  bool waitingAck;
  String msgID;
};
#define MAX_PENDING 5
PendingMsg pendingMsgs[MAX_PENDING];
unsigned long ackTimeout   = 1500;
int           maxRetries   = 4;
unsigned long nextMsgCounter = 0;

// =======================
// 🧭 Máquina de estados
// =======================
enum DroneState {
    IDLE,
    ARMING,
    READY_FOR_MISSION,
    PREPARE_TAKEOFF,
    TAKEOFF,
    NAVIGATE,
    STABILIZE,
    WAIT_ANALYSIS,
    RETURN_HOME,
    LAND,
    COMPLETE
};

DroneState state = IDLE;
unsigned long stateEntryTime    = 0;
unsigned long insideRadiusSince = 0;

// Para control del STATUS
DroneState lastSentState = IDLE;
bool statusDirty         = true;

void resetMissionState();
void sendStatusToGS(DroneState st);
void simulateDroneMotion();

void checkMissionChunkTimeout() {
    if (!missionHasHeader || missionReady) return;

    if (millis() - missionLastChunkTime > MISSION_TIMEOUT) {
        for (int i = 0; i < missionExpectedChunks; i++) {
            if (!missionChunkReceived[i]) {
                Serial.printf("⛔ Falta chunk %d → solicitando reenvío\n", i);
                // construir REQ_WP_CHUNK
                StaticJsonDocument<128> doc;
                doc["t"] = "REQ_WP_CHUNK";
                JsonObject d = doc.createNestedObject("d");
                d["i"] = i;

                String payload;
                serializeJson(doc, payload);
                String frame = String(UAV_HDR) + payload + SFX;

                LoRa.beginPacket();
                LoRa.print(frame);
                LoRa.endPacket();

                // Reiniciar el reloj para volver a chequear luego
                missionLastChunkTime = millis();
                return;  // pedimos 1 por vez
            }
        }
    }
}

void sendMissionError(const char* msg) {
    StaticJsonDocument<128> doc;
    doc["t"] = "MISSION_ERROR";
    JsonObject d = doc.createNestedObject("d");
    d["error"] = msg;

    String p;
    serializeJson(doc, p);
    String frame = String(UAV_HDR) + p + SFX;

    LoRa.beginPacket();
    LoRa.print(frame);
    LoRa.endPacket();
}


// ============================================================================
// 📡 Enviar estado de la FSM a la Ground Station
// ============================================================================
// Convierte el estado de la FSM a texto legible
String fsmStateToString(int s) {
  switch (s) {
    case IDLE:              return "IDLE";
    case ARMING:            return "ARMING";
    case READY_FOR_MISSION: return "READY_FOR_MISSION";
    case PREPARE_TAKEOFF:   return "PREPARE_TAKEOFF";
    case TAKEOFF:           return "TAKEOFF";
    case NAVIGATE:          return "NAVIGATE";
    case STABILIZE:         return "STABILIZE";
    case WAIT_ANALYSIS:     return "WAIT_ANALYSIS";
    case RETURN_HOME:       return "RETURN_HOME";
    case LAND:              return "LAND";
    case COMPLETE:          return "COMPLETE";
    default:                return "UNKNOWN";
  }
}

void sendStatusToGS(DroneState st) {

  if (st == lastSentState && !statusDirty)
    return;

  lastSentState = st;
  statusDirty   = false;

  // ----- Construimos JSON -----
  StaticJsonDocument<128> doc;
  doc["t"]       = "STATUS";
  doc["message"] = fsmStateToString((int)st);
  doc["ts"]      = millis();

  String payload;
  serializeJson(doc, payload);

  // ----- Generamos un msgID único -----
  String msgID = generateMsgID();   // ← ya existe en tu sistema

  // ----- Construimos el frame completo -----
  String frame = String(UAV_HDR) + payload + SFX;   // ej: "UAV#{json}#END"

  // ----- Envio usando ACK -----
  sendWithAck(frame, msgID);

  Serial.println("📤 STATUS enviado (ACK): " + fsmStateToString((int)st));
}


// Análisis RPi
enum AnalysisResult { NONE, GO, FIRE, PERSON };
AnalysisResult analysisResult = NONE;

// Misión / recorrido
int currentWaypoint = 0;
vector<Coordinate> pathPoints;

// Timeout análisis
const unsigned long ANALYSIS_TIMEOUT = 6000;
unsigned long analysisStartTime = 0;

// Comandos por LoRa
bool loraReturnCommand = false;
bool loraDisarmCommand = false;

// ⭐ MODO TEST (vuelo simulado sin mover motores)
bool testMode = false;

// Modo simulación
bool simulationMode = false;

// Heartbeat Pixhawk
unsigned long lastHeartbeatMs = 0;

// ============================================================================
// 🛰️ FILTRO GPS (mediana + warmup + rechazo de saltos)
// ============================================================================
double median4(double a, double b, double c, double d) {
  double arr[4] = {a,b,c,d};
  for (int i = 0; i < 3; i++)
    for (int j = i + 1; j < 4; j++)
      if (arr[j] < arr[i]) {
        double t = arr[i]; arr[i] = arr[j]; arr[j] = t;
      }
  return (arr[1] + arr[2]) / 2.0;
}

void filterGPS(double lat, double lon, double alt,
               double &lat_out, double &lon_out, double &alt_out) {

  if (fabs(lat) < 0.0001 && fabs(lon) < 0.0001)
    return;

  lat_window[win_idx] = lat;
  lon_window[win_idx] = lon;
  alt_window[win_idx] = alt;
  win_idx = (win_idx + 1) % 4;

  double lat_m = median4(lat_window[0], lat_window[1], lat_window[2], lat_window[3]);
  double lon_m = median4(lon_window[0], lon_window[1], lon_window[2], lon_window[3]);

  if (!have_filter) {
    lat_f = lat_m; lon_f = lon_m; alt_f = alt;
    have_filter = true;
    gpsWarmup = 0;
    Serial.println("[GPS] 🆗 Filtro inicializado");
  }
  else {
    gpsWarmup++;
    if (gpsWarmup < 200) {
      lat_f = 0.7 * lat_m + 0.3 * lat_f;
      lon_f = 0.7 * lon_m + 0.3 * lon_f;
      alt_f = 0.5 * alt + 0.5 * alt_f;

      double dLat = fabs(lat_m - lat_f);
      double dLon = fabs(lon_m - lon_f);
      static int stableCount = 0;
      if (dLat < 0.00002 && dLon < 0.00002) {
        stableCount++;
        if (stableCount >= 8) {
          gpsWarmup = 9999;
          Serial.println("[GPS] ✅ Estabilización completada");
        }
      }
    } else {
      if (fabs(lat_m - lat_f) > MAX_JUMP_DEG || fabs(lon_m - lon_f) > MAX_JUMP_DEG) {
        Serial.println("[GPS] ⚠️ Salto descartado");
        lat_out = lat_f; lon_out = lon_f; alt_out = alt_f;
        return;
      }
      lat_f = 0.25 * lat_m + 0.75 * lat_f;
      lon_f = 0.25 * lon_m + 0.75 * lon_f;
      alt_f = 0.25 * alt    + 0.75 * alt_f;
    }
  }

  lat_out = lat_f;
  lon_out = lon_f;
  alt_out = alt_f;
}

// ============================================================================
// 🌎 Utils geodésicos
// ============================================================================
double deg2rad(double deg) { return deg * M_PI / 180.0; }
double rad2deg(double rad) { return rad * 180.0 / M_PI; }

double haversineDistance(double la1, double lo1, double la2, double lo2) {
  double R = 6371000.0;
  double dLat = deg2rad(la2 - la1);
  double dLon = deg2rad(lo2 - lo1);
  double a = sin(dLat/2)*sin(dLat/2) +
             cos(deg2rad(la1))*cos(deg2rad(la2))*sin(dLon/2)*sin(dLon/2);
  double c = 2 * atan2(sqrt(a), sqrt(1-a));
  return R * c;
}

double computeBearing(double la1, double lo1, double la2, double lo2) {
  double y = sin(deg2rad(lo2 - lo1)) * cos(deg2rad(la2));
  double x = cos(deg2rad(la1))*sin(deg2rad(la2)) -
             sin(deg2rad(la1))*cos(deg2rad(la2))*cos(deg2rad(lo2 - lo1));
  double brng = atan2(y, x);
  return fmod((rad2deg(brng) + 360.0), 360.0);
}

// ============================================================================
// 📡 ACKs LoRa – helpers
// ============================================================================
String generateMsgID() {
  nextMsgCounter++;
  return String(nextMsgCounter);
}

void sendWithAck(const String &jsonPayload, const String &id) {
  String full = jsonPayload;
  if (!jsonPayload.startsWith("UAV#")) full = "UAV#" + jsonPayload;
  if (!full.endsWith("#END")) full += "#END";

  LoRa.beginPacket();
  LoRa.print(full);
  LoRa.endPacket();

  for (int i = 0; i < MAX_PENDING; i++) {
    if (!pendingMsgs[i].waitingAck) {
      pendingMsgs[i].payload    = full;
      pendingMsgs[i].lastSend   = millis();
      pendingMsgs[i].retries    = maxRetries;
      pendingMsgs[i].waitingAck = true;
      pendingMsgs[i].msgID      = id;
      return;
    }
  }
  Serial.println("⚠️ Cola ACK llena");
}

void handleAck(const String &ackID) {
  for (int i = 0; i < MAX_PENDING; i++) {
    if (pendingMsgs[i].waitingAck && pendingMsgs[i].msgID == ackID) {
      String tipo = "Desconocido";
      int posT = pendingMsgs[i].payload.indexOf("\"t\":\"");
      if (posT >= 0) {
        int posEnd = pendingMsgs[i].payload.indexOf("\"", posT + 5);
        if (posEnd > posT) tipo = pendingMsgs[i].payload.substring(posT + 5, posEnd);
      }

      //Serial.print("✅ [ACK] ID="); Serial.print(ackID);
     // Serial.print(" (Tipo=");      Serial.print(tipo);
      //Serial.println(")");

      pendingMsgs[i].waitingAck = false;
      pendingMsgs[i].payload = "";
      pendingMsgs[i].msgID   = "";
      return;
    }
  }
 // Serial.print("⚠️ [ACK desconocido] ID="); Serial.println(ackID);
}

void checkPendingAcks() {
  unsigned long now = millis();
  for (int i = 0; i < MAX_PENDING; i++) {
    if (!pendingMsgs[i].waitingAck) continue;

    if (now - pendingMsgs[i].lastSend > ackTimeout) {
      if (pendingMsgs[i].retries > 0) {
        LoRa.beginPacket();
        LoRa.print(pendingMsgs[i].payload);
        LoRa.endPacket();

        pendingMsgs[i].lastSend = now;
        pendingMsgs[i].retries--;

        String tipo = "Desconocido";
        int posT = pendingMsgs[i].payload.indexOf("\"t\":\"");
        if (posT >= 0) {
          int posEnd = pendingMsgs[i].payload.indexOf("\"", posT + 5);
          if (posEnd > posT) tipo = pendingMsgs[i].payload.substring(posT + 5, posEnd);
        }

       // Serial.print("🔁 [Reintento ACK] ID=");
       // Serial.print(pendingMsgs[i].msgID);
        //Serial.print(" Tipo="); Serial.print(tipo);
       // Serial.print(" quedan "); Serial.print(pendingMsgs[i].retries);
       // Serial.println(" intentos");
      } else {
       // Serial.print("❌ [ACK perdido] ID=");
       // Serial.print(pendingMsgs[i].msgID);
       // Serial.print(" payload="); Serial.println(pendingMsgs[i].payload);

        pendingMsgs[i].waitingAck = false;
        pendingMsgs[i].payload = "";
        pendingMsgs[i].msgID   = "";
      }
    }
  }
}

void sendAckToGS(const String &id) {
    if (id == "") {
        Serial.println("⚠️ ACK sin ID");
        return;
    }

    StaticJsonDocument<128> doc;
    doc["t"] = "ACK";
    doc["id"] = id;        // 🔥 ID AL NIVEL SUPERIOR
    doc["ts"] = millis();

    String p;
    serializeJson(doc, p);

    String msg = String(UAV_HDR) + p + String(SFX);

    LoRa.beginPacket();
    LoRa.print(msg);
    LoRa.endPacket();

    // Debug opcional
    // Serial.println("📤 ACK → " + msg);
}

void sendJsonNoAckToGS(const JsonDocument &doc) {
  String payload;
  serializeJson(doc, payload);
  String frame = String(UAV_HDR) + payload + String(SFX);

  LoRa.beginPacket();
  LoRa.print(frame);
  LoRa.endPacket();
}

// ============================================================================
// 📡 TELEMETRÍA Y EVENTOS HACIA GS
// ============================================================================
void sendTelemetry(double lat,double lon,double alt,double speed,double heading,unsigned long ts) {
    StaticJsonDocument<256> doc;
    doc["t"] = "TELEMETRY";

    JsonObject d = doc.createNestedObject("d");
    d["lat"]     = lat;
    d["lon"]     = lon;
    d["alt"]     = alt;
    d["speed"]   = speed;
    d["heading"] = heading;

    // Datos reales desde MAVLink
    d["battery"] = mav_batt_remaining;      // %
    d["voltage"] = mav_batt_voltage;        // V
    d["armed"]   = mav_armed;               // true/false
    d["mode"]    = decodeFlightMode(mav_custom_mode);

    // 🔥 NUEVO: alerta por voltaje bajo
    const float LOW_VOLTAGE_THRESHOLD = 11.1; 
    bool warn = (mav_batt_voltage > 0) && (mav_batt_voltage < LOW_VOLTAGE_THRESHOLD);
    d["batt_warn"] = warn;

    doc["ts"]    = ts;

    String p;
    serializeJson(doc,p);
    String msg = String(UAV_HDR) + p + String(SFX);

    LoRa.beginPacket();
    LoRa.print(msg);
    LoRa.endPacket();
}



void sendEventToGS(const String &type, double lat, double lon, double alt, 
                   unsigned long wpIndex, float temperature) 
{
  // ----- Construimos JSON -----
  StaticJsonDocument<256> doc;
  doc["t"]       = type;      // Ej: "EVENT_FIRE", "EVENT_PERSON", etc.
  doc["lat"]     = lat;
  doc["lon"]     = lon;
  doc["alt"]     = alt;
  doc["wp"]      = wpIndex;
  doc["temp"]    = temperature;
  doc["ts"]      = millis();

  String payload;
  serializeJson(doc, payload);

  // ----- Generamos msgID único -----
  String msgID = generateMsgID();

  // ----- Armamos frame UAV#...#END -----
  String frame = String(UAV_HDR) + payload + SFX;

  // ----- Envío por ACK -----
  sendWithAck(frame, msgID);

  Serial.println("📤 EVENT enviado (ACK): " + type);
}


// ============================================================================
// 🔎 Extracción de frames LoRa (GS#...#END)
// ============================================================================
bool extractNextFrame(String &buf, String &jsonOut, const char* wantedHdr) {
  int h  = buf.indexOf(wantedHdr);
  int hU = buf.indexOf(UAV_HDR);

  if (hU >= 0 && (hU < h || h < 0)) {
    int endU = buf.indexOf(SFX, hU);
    if (endU < 0) return false;
    buf.remove(0, endU + strlen(SFX));
    return false;
  }

  if (h < 0) {
    if (buf.length() > 2048)
      buf.remove(0, buf.length() - 256);
    return false;
  }

  int lbrace = buf.indexOf('{', h);
  if (lbrace < 0) return false;
  int end = buf.indexOf(SFX, lbrace);
  if (end < 0) return false;

  jsonOut = buf.substring(lbrace, end);
  buf.remove(0, end + strlen(SFX));
  jsonOut.trim();
  return true;
}
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
void loop() {

    unsigned long now = millis();

    handleLoRa(); 

    checkPendingAcks();

    readMavlink();

    handleSerialRPI();

    updateStateMachine();

    if (now - lastHbMs > 1000) {
        sendHeartbeatToPixhawk();
        lastHbMs = now;
    }

    handleTelemetry();

    checkMissionChunkTimeout();

    simulateDroneMotion();

    handleServoAction();
}

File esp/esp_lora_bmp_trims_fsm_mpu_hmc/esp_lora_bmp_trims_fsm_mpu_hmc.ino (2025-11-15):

// ============================================================================
// 📡 DRON BUSCADOR TÉRMICO – TELEMETRÍA LoRa + GPS + BMP280
// Organización modular y comentarios por bloques funcionales
// ============================================================================

#include <SPI.h>
#include <LoRa.h>
#include <TinyGPS++.h>
#include <ArduinoJson.h>
#include <Adafruit_BMP280.h>
#include <Preferences.h>
#include <math.h>
#include <units.h>
#include <mpu9250.h>
#include <eigen.h>
#include <Wire.h>
#include <Adafruit_Sensor.h>
#include <Adafruit_HMC5883_U.h>

// ============================================================================
// 🛰️ CONFIGURACIÓN DE HARDWARE
// ============================================================================

// --- GPS ---
#define GPS_RX 16
#define GPS_TX 17
HardwareSerial SerialGPS(2);
TinyGPSPlus gps;
Preferences gpsPrefs;

// --- BMP280 ---
Adafruit_BMP280 bmp;
bool bmp_ok = false;

// --- LoRa ---
#define LORA_CS 5
#define LORA_RST 14
#define LORA_IRQ 27
#define LORA_BAND 433E6

static const char* GS_HDR  = "GS#";
static const char* UAV_HDR = "UAV#";
static const char* SFX     = "#END";

String loraRxBuf;

// --- UART Raspberry ---
#define RPI_RX  32
#define RPI_TX  33
HardwareSerial SerialRPI(1);
#define RPI_BUFFER_SIZE 256
#define RPI_TIMEOUT_MS  50
char rpiBuffer[RPI_BUFFER_SIZE];
size_t rpiIndex = 0;
bool receivingJson = false;

// --- IMU MPU9250 ---
bfs::Mpu9250 mpu(&Wire, bfs::Mpu9250::I2C_ADDR_PRIM);
bool mpuReady = false;
Adafruit_HMC5883_Unified magExt = Adafruit_HMC5883_Unified(12345);
bool magReady = false;

// Estado angular
unsigned long lastIMUUpdate = 0;

// → Ajuste de declinación magnética para Adrogué / Buenos Aires
const float MAG_DECLINATION_DEG = -9.9f;
unsigned long lastAttPrint = 0;
const unsigned long ATT_PRINT_INTERVAL = 500; 

// --- Filtros EMA (suavizado) ---
#define ALPHA_ACC  0.15f
#define ALPHA_GYRO 0.15f
#define ALPHA_MAG  0.20f
#define ALPHA_YAW  0.05f   // fusión: 0.05 = 95% giro + 5% compás

// Variables filtradas globales
float ax_f=0, ay_f=0, az_f=0;
float gx_f=0, gy_f=0, gz_f=0;
float mx_f=0, my_f=0, mz_f=0;

// Salidas globales
float roll=0, pitch=0, yaw_f=0;
float yawGyro = 0;
float yawMag = 0;

// ========================================================
//  🔧 CALIBRACIÓN MAGNÉTICA PRO (ellipsoid fitting)
// ========================================================

#define MAX_MAG_SAMPLES 1200   // hasta ~10 segundos
struct MagSample {
  float x, y, z;
};

MagSample magBuff[MAX_MAG_SAMPLES];
int magCount = 0;
bool magCalActivePRO = false;
unsigned long magCalStartPRO = 0;
unsigned long magCalDurationPRO = 0;


// ============================================================
// ESTRUCTURAS BÁSICAS
// ============================================================
struct Coordinate {
  double lat;
  double lon;
};

struct Mission {
  bool loaded = false;
  std::vector<Coordinate> polygon;
  Coordinate home;
  double altitude = 0;
  double spacing  = 0;
  String event_action;
} mission;

struct MagAxis {
  float minVal;
  float maxVal;
};

struct MagCalAxisData {
  bool active;
  unsigned long startMs;
  unsigned long durationMs;
  size_t samples;
  MagAxis x, y, z;
};

MagCalAxisData magCal;

String magQuality = "GOOD";
struct IMUCalibration {
  float accelBias[3];
  float gyroBias[3];
  float magBias[3];
  float magScale[3];
};

// Variable global que contiene los datos actuales de calibración
IMUCalibration imuCal;

struct PIDParams {
  float kp;
  float ki;
  float kd;
};

struct PIDSet {
  PIDParams accel;
  PIDParams roll_lr;
  PIDParams roll_fb;
  PIDParams rudder;
};

PIDSet pidConfig;   // configuración actual de PID

// ============================================================
// 🧭 Máquina de estados del dron
// ============================================================

enum DroneState {
  IDLE,            // Esperando misión
  TAKEOFF,         // Ascendiendo hasta altitud deseada
  NAVIGATE,        // Avanzando a waypoint
  STABILIZE,       // Estabilizando cámaras y enviando STABLE
  WAIT_ANALYSIS,   // Esperando respuesta del RPi
  RETURN_HOME,     // Retorno al punto HOME
  LAND,            // Descendiendo
  COMPLETE         // Misión finalizada
};

DroneState state = IDLE;
unsigned long stateEntryTime = 0;

// Resultado de análisis de la RPi
enum AnalysisResult { NONE, GO, FIRE, PERSON };
AnalysisResult analysisResult = NONE;

// Misión y recorrido
int currentWaypoint = 0;
std::vector<Coordinate> pathPoints;

// Timeout de análisis (90 s)
const unsigned long ANALYSIS_TIMEOUT = 90000;
unsigned long analysisStartTime = 0;

// Interrupciones por LoRa
bool loraReturnCommand = false;
bool loraDisarmCommand = false;

// Para telemetría / misión
unsigned long missionStartTime = 0;
// --- SIMULACIÓN ---
bool simulationMode = false;

// ============================================================================
// ⚙️ CONFIGURACIÓN DE PREFS
// ============================================================================
Preferences prefs;
struct TrimValues {
  float accel   = 128.0;
  float roll_lr = 128.0;
  float roll_fb = 128.0;
  float rudder  = 128.0;
  float sw      = 128.0;
} trims;

void loadTrims() {
  prefs.begin("drone", true);
  trims.accel   = prefs.getFloat("accel", 128.0);
  trims.roll_lr = prefs.getFloat("roll_lr", 128.0);
  trims.roll_fb = prefs.getFloat("roll_fb", 128.0);
  trims.rudder  = prefs.getFloat("rudder", 128.0);
  trims.sw      = prefs.getFloat("switch", 128.0);
  prefs.end();
}

void saveTrims() {
  prefs.begin("drone", false);
  prefs.putFloat("accel", trims.accel);
  prefs.putFloat("roll_lr", trims.roll_lr);
  prefs.putFloat("roll_fb", trims.roll_fb);
  prefs.putFloat("rudder", trims.rudder);
  prefs.putFloat("switch", trims.sw);
  prefs.end();
}

void saveIMUCalibration() {
  prefs.begin("mpu9250", false);
  prefs.putBytes("accelBias", imuCal.accelBias, sizeof(imuCal.accelBias));
  prefs.putBytes("gyroBias",  imuCal.gyroBias,  sizeof(imuCal.gyroBias));
  prefs.putBytes("magBias",   imuCal.magBias,   sizeof(imuCal.magBias));
  prefs.putBytes("magScale",  imuCal.magScale,  sizeof(imuCal.magScale));
  prefs.end();
  Serial.println("💾 Calibraciones IMU guardadas");
}

void loadIMUCalibration() {
  prefs.begin("mpu9250", true);
  prefs.getBytes("accelBias", imuCal.accelBias, sizeof(imuCal.accelBias));
  prefs.getBytes("gyroBias",  imuCal.gyroBias,  sizeof(imuCal.gyroBias));
  prefs.getBytes("magBias",   imuCal.magBias,   sizeof(imuCal.magBias));
  prefs.getBytes("magScale",  imuCal.magScale,  sizeof(imuCal.magScale));
  prefs.end();
  Serial.println("📥 Calibraciones IMU cargadas");
}

void savePID() {
  prefs.begin("pidConfig", false);
  size_t written = prefs.putBytes("config", &pidConfig, sizeof(pidConfig));
  prefs.end();
  Serial.printf("💾 Guardado PID (%u bytes de %u)\n", written, sizeof(pidConfig));
}
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

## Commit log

2025-08-19 Create Gant - Proyecto.mpp
    Cree el gant del proyecto. Las fechas son arbitrarias y bastante optimistas, Cuando puedan, denle una ojeada por si quieren corregir algo o sino lo vemos juntos el jueves y ya lo definimos para poder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
2025-08-31 modelado 3d imprimibles
    base y patas tren aterrizaje
    [Ensamblaje tren aterrizaje.SLDASM, base.SLDPRT, base.STL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]
2025-08-31 Update Ensamblaje tren aterrizaje.SLDASM
    [Ensamblaje tren aterrizaje.SLDASM]
2025-09-02 Create Fernandez-Moscariello-Yacono - Diagrama de Gantt.docx
2025-09-02 Create Fernandez-Moscariello-Yacono - Diagrama de Gantt.pdf
2025-09-04 Create Area de cobertura MLX90640.dwg
    [Area de cobertura MLX90640.dwg]
2025-09-27 Create fotoM5_fotoCSI_12_funca.py
    si se dispara un alerta desde la camara temografica, se toma una foto con la CSI. Todo ejecutado desde la raspi
2025-09-27 gs stable
    [Pieza13.STL, Pieza13.sldprt, Pieza16.STL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]
2025-09-29 Create phM5_phCSI_UART_14_funca.py
    Create phM5_phCSI_UART_14_funca.py
    Envio de .json "PERSON" y "FIRE" desde la raspi a esp32. usando UART 2
2025-10-06 estable 6-10
    [antenagps.SLDPRT, antenagps.STL, antenalora.SLDPRT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]
2025-10-15 Create Deteccion_claude_17.py
    Version de la detección, actualizada al 15/10
2025-10-29 .
    imagenes generadas
    [Carcaza.SLDPRT, Carcaza.STL, M5 Stick.SLDPRT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]
2025-11-17 servo, wp, status
2025-11-23 gs satelital, fixes frecuencia arm, datos y loop, logos dron y waypoint para revisar
2025-11-23 Create prog7_testmode1.ino
    Cambio para test mode
2025-11-25 Version final
    Prog10_ACKStatus es la version final
2025-11-29 modelado 3d ordenado
    [Base superior.SLDPRT, Base superior.STL, Buje .SLDPRT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]
2025-11-29 solo programas funcionales a fecha de regularidad
2025-12-02 ensamblae cuerpo compleot
    [Coso para transportar.SLDPRT, Coso para transportar.STL, Ensamblaje1.SLDASM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]
2025-12-02 Codigo final v1
    Se modifico el calculo de wp y como se envian
2025-12-02 modelo camaras
    [Area de cobertura MLX90640.dwg, Carcaza.SLDPRT, Carcaza.STEP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]
2025-12-07 modelado base v2
    [Sólido1.sldprt, Sólido2.sldprt, base2.SLDPRT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]
2025-12-10 bat failsafe, path compare
    [prog12_poligono_home_failsafe_bat.ino]
2025-12-15 diagramas electricos y de bloques
2025-12-15 pata reforzada
    [Simetríapata45^Ensamblaje1.STL, Simetríapata45^Ensamblaje1.sldprt, pata45^Ensamblaje1.STL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]
2025-12-16 Informe final
    [A2-ASECON 2024.SLDDRW, A3-ASECON 2024.SLDDRW, A4-ASECON 2024.SLDDRW]
2025-12-18 hojas de datos completo
